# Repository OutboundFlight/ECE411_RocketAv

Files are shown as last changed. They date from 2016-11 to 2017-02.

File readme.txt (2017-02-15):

Overview:

This GitHub provides documentation for the design, implemation, and use of the TinyAV
Amateur Avionics System. The TinyAV is a printed circuit board that includes a 
microcontroller, acellerometer, gyroscope, temperature sensor, flash
memory storage, and a rechargeable lithium-ion battery. It allows for a portable way 
to record flight data that can be use for flight analysis on model rockets.

----------------------------------------------------------------------------------------------

Table Of Contents:

Assignments - Team exercises assigned in ECE 411
Doc         - Project Proposals, Project Requirements, UML Diagrams, Testing Documentation, 
	      Project Schedules, & Bill Of Materials
Eagle       - Schematic & Board Layout Documentation
Launch_Data - Test Launch Raw Data & Analysis Graphs
Ref	    - Reference Documentation For Board Creation
Src	    - Libraries & Source Code For The TinyAv Board

----------------------------------------------------------------------------------------------

Useful Links:

Lab for Interconnected Devices: http://psu-epl.github.io/
Arduino Software: https://www.arduino.cc/

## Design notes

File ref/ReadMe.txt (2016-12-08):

Raw Setup:
-------------------------------------------------------------------------------------------------------------
PCB Creation:

1) In Eagle, use DRC > Masks to set Cream min to 5.5 mil and max to 7mil.Make sure this actually adjusts cream field sizes! 
   The comparator footprint in the TI library is wronng.
2) Export to gerber files.  Use the cream gerber layer to create the stencil.
3) Use the Full Spectrum Professional Series CO2 20x12 Laser to vector cut.
	Laser Settings:
	Vector Speed: 80%
	Vector Current: 20%
	Power: 0.2%
4) Line up stencil on board and secure.  Apply solder paste on PCB using the stencil as aid. 
	Tips: 
	1) Take the syringe tip off of the solder paste syringe
	2) Spread ~2-3 lines of solder paste, just above the stencil
	3) Using a Solder Spreader card, slowly spread the paste over the board (try to only swipe once!)
5) Place components.
6) Use the Torch T200N Reflow Oven to melt solder paste and secure components.

References:

Laser Cutter: https://github.com/psu-epl/psu-epl.github.com/wiki/Lasercutter
Reflow Oven:  https://github.com/psu-epl/psu-epl.github.com/wiki/Torch-T200N-Reflow-Oven 
-------------------------------------------------------------------------------------------------------------
Bootloader:

1) Plug in Dragon AVR (Located in FAB60-04).
2) Open AtmelStudio.
3) Under Tools, go to Device Programming.
4) Select DragonAVR-Atmega32U4-ISP.
5) Apply.
6) Click Check and verify the voltage.
7) Go to Memory-Flash.
8) Browse for Caterina-lilypadusb.hex in given GitHub folder.
9) Click Program.
10) After programming, go to Fuse and set the fuses to the following:
	Extended byte: 0xCE
	High byte:     0xD0
	Low byte:      0xFF
11) Go to Lock Bit and set it to 0xFF.
12) The bootloader should now be on the TinyAv.
-------------------------------------------------------------------------------------------------------------
Programming:

1) Once bootloader is on TinyAv, it can now be plugged into a USB port (via MicroUSB).
2) Under Device Manager in Windows, the TinyAV should be seen as a port named Lilypad USB.
3) Arduino IDE sketches can now be uploaded to the TinyAV using:
	Board: Arduino USB
	Port: Lilypad USB (COMX)
	Programmer: AVRISP mkll
4) Go to Sketch>Include Library and include the the 3 .zip libraries located in the src folder:
	Adafruit_LSM9DS0_Library-master.zip
	Adafruit_Sensor-master.zip
	tinyav.zip
5) Go to File>Open and open the RocketAv arduino sketch located in the src folder.
6) Ensure the Lilypad is powered on, plugged in via microUSB, and is detected under Tools>Ports
7) Upload the sketch on Arduino IDE
--------------------------------------------------------------------------------------------------------------
Launch Procedure:

1) Set up rocket
2) Turn on the tinyav board. Connect to USB port.
3) Get IMU sample data:
	Ensure xm is calibrated correctly (1g should be about integer 2000)
	Check sample rate
4) Upload correct sketch:
	Ensure the arduino sketch is not in debug mode
	Set a launch countdown timer in the sketch
5) Erase the memory chip
6) Insert motor with igniter. 
7) Set the arduino into launch mode. Start a stopwatch.
8) Detach the USB cable.
9) Place the tinyav board in the rocket.
10) Attach ignition control leads to igniter leads.
11) Clear launch zone.
12) Launch.

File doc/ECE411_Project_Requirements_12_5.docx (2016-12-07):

Tiny Avionics

PRODUCT DESIGN SPECIFICATION

Version 3.0

12/06/2016

Aaron Baker, Andy Rusinek, Daniel Schaeffer, Minh-Nhut Dang

REVISION HISTORY
REVISION | DESCRIPTION | DATE
1.0 | INITIAL RELEASE | 10/25/2016
2.0 | PROJECT NAME CHANGE | 12/01/2016
3.0 | UPDATED REQUIREMENTS TEXT | 12/06/2016

TABLE OF CONTENTS

1 PROJECT OVERVIEW

1.1 BACKGROUND

1.2 OVERVIEW

2 REQUIREMENTS

2.1 FUNCTIONALITY

2.2 PHYSICAL RESTRICTIONS

2.3 DOCUMENTATION

2.4 ECONOMICS

2.5 MARKETING

2.6 GENERAL

1 PROJECT OVERVIEW

1.1 BACKGROUND

This project will develop a rocket avionics system for small model rockets. After we design a working version, we plan to create sellable kits which others becoming interested in amateur rocketry can use. On the system, we will have sensors for attitude and acceleration during flight, which will be processed on board and stored in a memory chip. The data will be retrievable after flight, and can then be processed on a computer and displayed visually.

1.2 OVERVIEW

The goal of our project is to create a small flight computer which can collect data in flight and store it for later analysis. To achieve this, we will use a micro-processor with the Arduino bootloader, an accelerometer, gyroscope, and an on-board flash memory chip. During flight, the gyroscope and accelerometer will gather data and save data to the onboard flash-memory chip. After flight, data will be able to be pulled off the flash memory and viewed through programs such as MATLAB and Excel. The system will be powered by a single rechargeable lithium-ion cell.

2 REQUIREMENTS

2.1 FUNCTIONALITY:

- Deploy recovery system for reusability of rocket and board.
- Accurately sense acceleration, attitude, and rotation to at least 3 significant digits
- Must have ample power management to last at least 10 consecutive 30 second flights.
- Record flight data at a sample rate of 1 kHz (acceleration, attitude, rotation) for retrieval after flight
- Be able to transfer data to computer for processing and display

2.2 PHYSICAL RESTRICTIONS:

- Must be 1x3 inches or smaller to fit inside rocket nose
- Durable through indefinite number of uses and crash landings
- Easily removed and reinserted into different type of rocket noses

2.3 DOCUMENTATION:

- Thoroughly documented schematics, PCB layouts, and design sketches with revision tracking
- General test plan for basic functionality of accelerometer and gyroscope
- Comprehensive User’s Manual for device operation and set-up

2.4 ECONOMICS:

- Total cost under $60
- Must use easy to obtain parts from reputable vendor

2.5 MARKETING

- Boards assembled easily and cheaply
- Easy to use built in test-programs and Arduino libraries for code development
- Raw data easily converted to visual in form of 2-D or 3-D plot
- Have LED indications of functioning parts

2.6 GENERAL

- Be visually appealing
- Be expandable
- Integratable into other amateur rocketry systems

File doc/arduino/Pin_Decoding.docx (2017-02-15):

Look at pin name on ATMEGA32U4 (i.e. PF1… PF0… ETC)

Find the pin name on the LEONARDO PINOUT picture

Find the Pin on the physical leonardo board corresponding with the PIN you want to decode…

I.e: PF0 = A5.

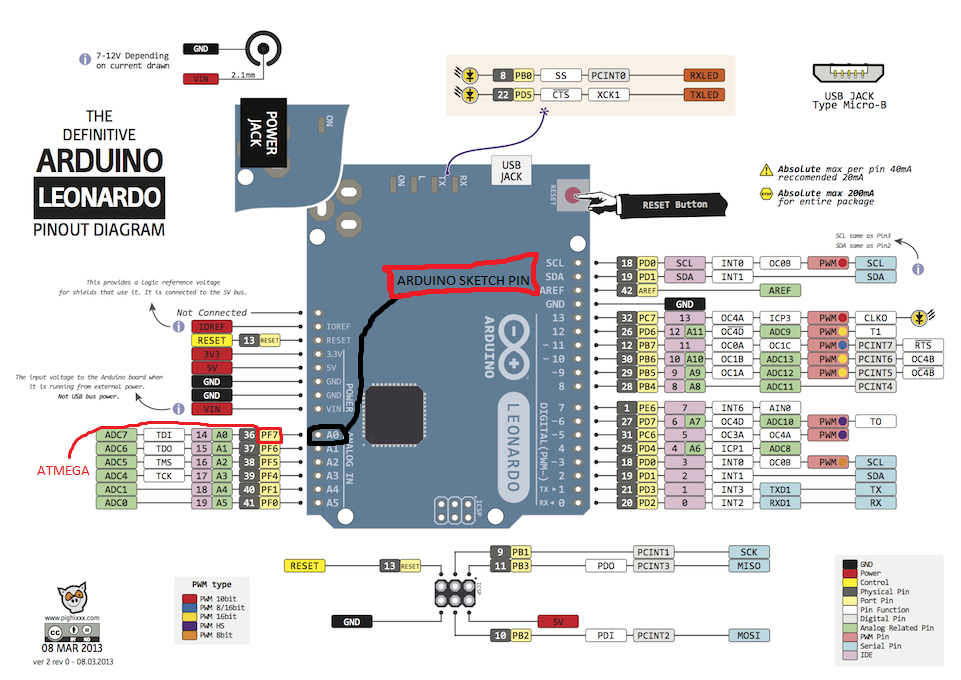
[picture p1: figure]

ATMEGA32U4 | ARDUINO SKETCH PIN NAME
MISO | 14
MOSI | 15
SCLK | 16
MEM_EN (PF1) | A4 (22)
XM_EN (PF4) | A3
GYR_EN (PF5) | A2
RED_LED (PB6) | 10
GREEN_LED (PB5) | 9
BLUE_LED (PB4) | 8

0xCE

0xD0

0xFF

0xFF

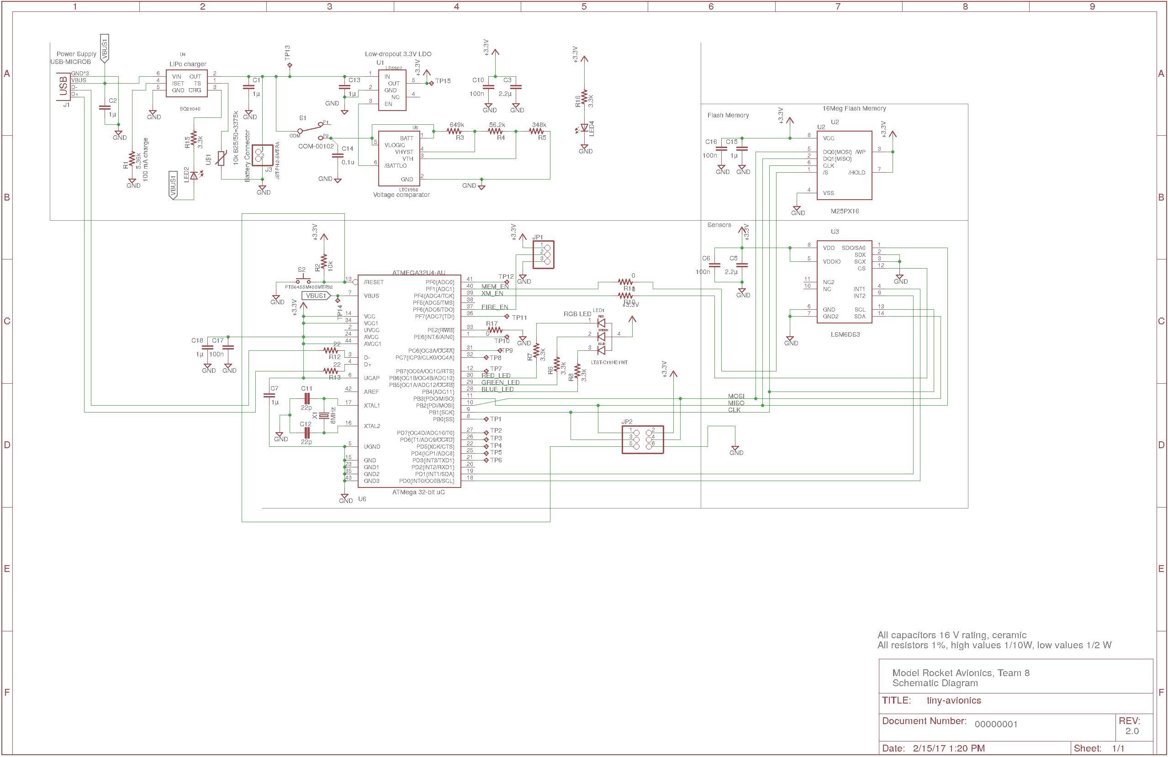
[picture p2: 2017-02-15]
eagle/schematic.png

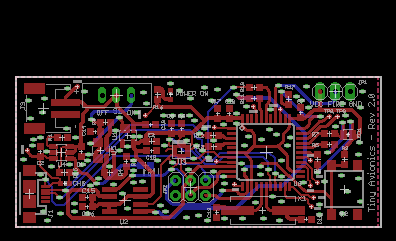
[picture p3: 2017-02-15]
eagle/board.png

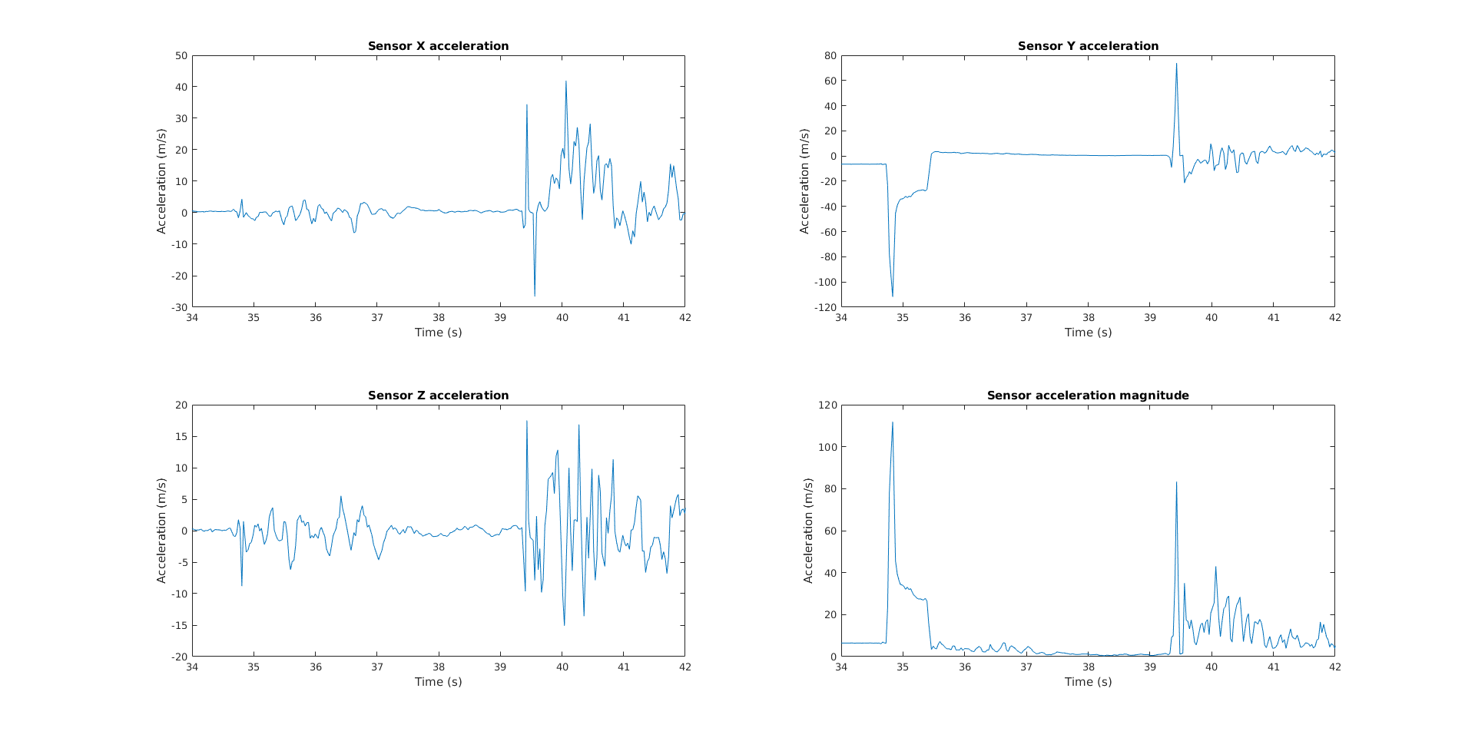
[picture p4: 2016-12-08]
launch_data/Launch 12-08-16/launch1_accel.png

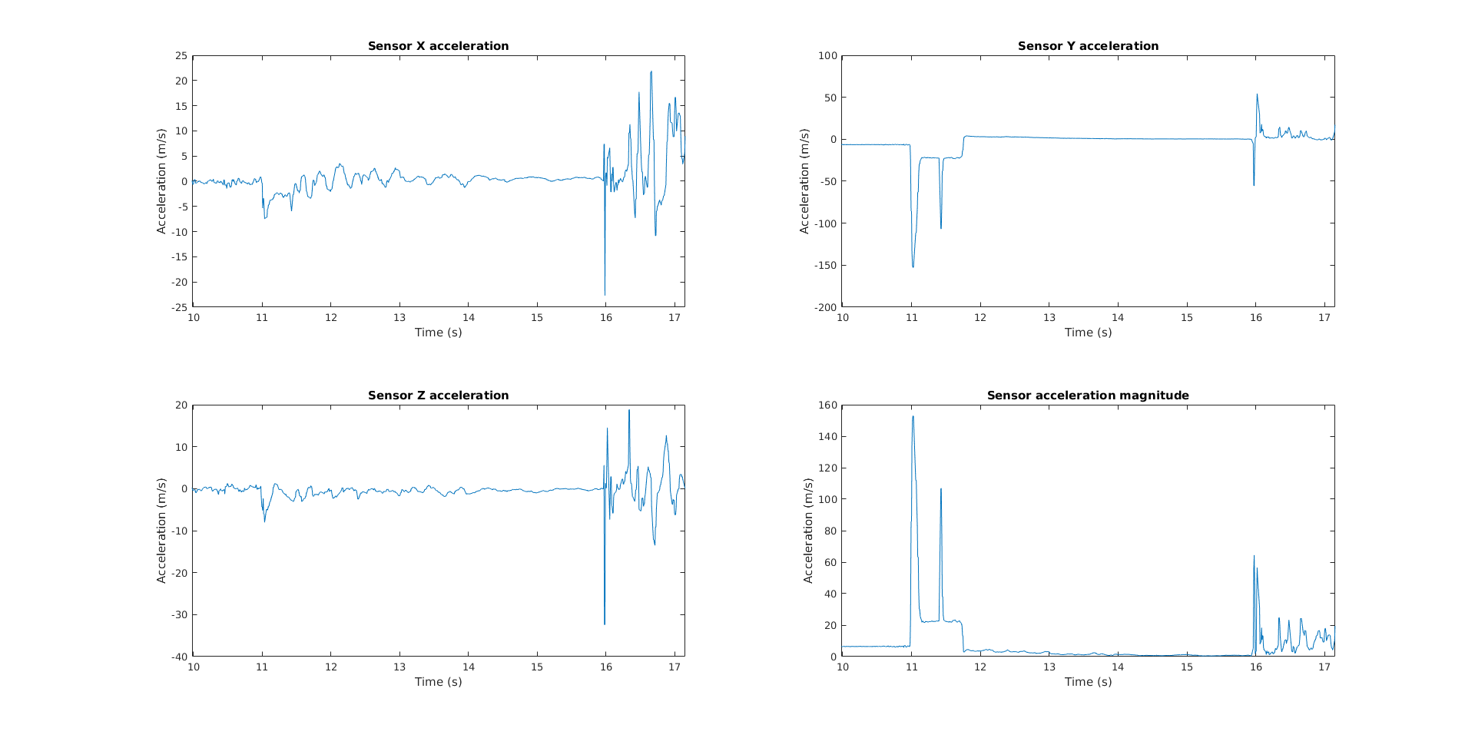
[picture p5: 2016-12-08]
launch_data/Launch 12-08-16/launch3_accel.png

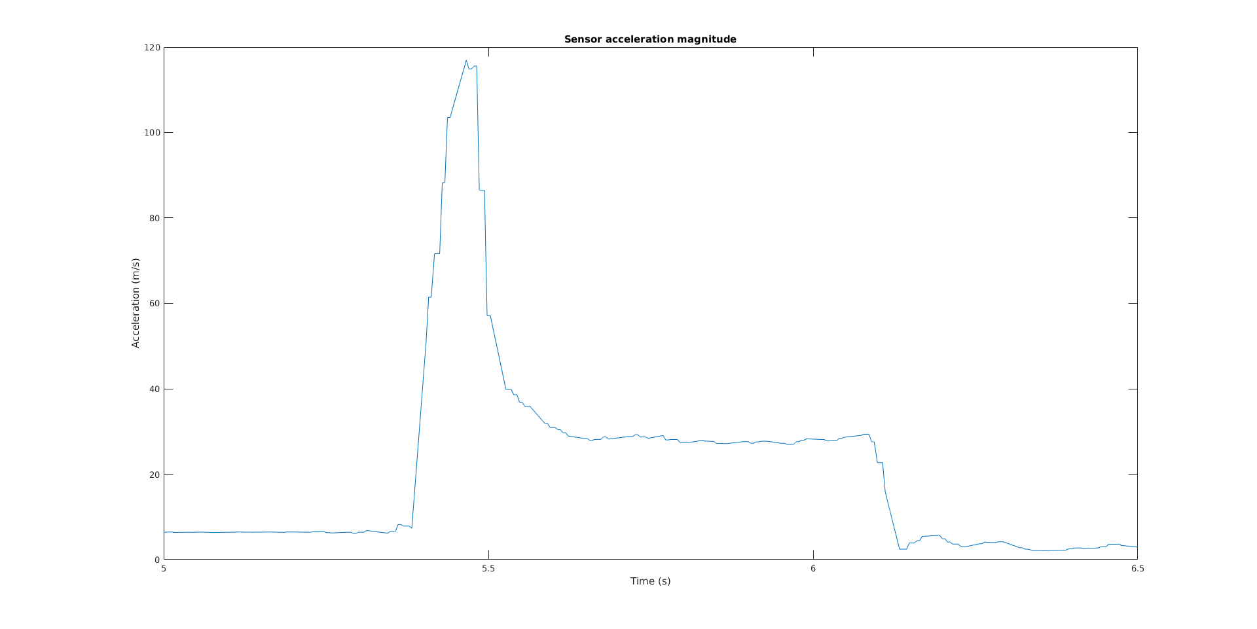
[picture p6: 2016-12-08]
launch_data/Launch 12-08-16/launch4_thrustcurve.png

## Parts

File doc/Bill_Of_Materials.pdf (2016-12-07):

QUANTITY/BRD | REF DES | DESCRIPTION | VENDOR | VENDOR_PN | PRICE(EA) (USD) | TOTAL
6 | C1, C2, C7, C13, C15, C18 | CAP CER 1UF 16V Y5V 0603 | DIGIKEY | 311-1372-1-ND | $0.10 | $0.60
2 | C11, C12 | CAP CER 22PF 16V NP0 0603 | DIGIKEY | 399-9031-1-ND | $0.10 | $0.20
1 | C3 | CAP CER 4.7UF 16V X5R 0603 | DIGIKEY | 587-2786-1-ND | $0.38 | $0.38
1 | C4 | CAP CER 0.22UF 16V X7R | DIGIKEY | 445-1318-1-ND | $0.10 | $0.10
2 | C5, C9 | CAP CER 2.2UF 16V Y5V 0603 | DIGIKEY | 587-1263-1-ND | $0.28 | $0.56
5 | C6, C10, C14, C16, C17 | CAP CER 0.1UF 16V X7R 0603 | DIGIKEY | 311-1088-1-ND | $0.10 | $0.50
1 IC1 | | IC LI-ION/LI-POL CHARGER 10-SON | DIGIKEY | 296-14397-1-ND | $2.97 | $2.97
1 | J1 | USB-MICROB | SPARKFUN | PRT-08533 | $1.50 | $1.50
1 | J3 | 455-1578-1-ND | DIGIKEY | 455-1578-1-ND | $0.43 | $0.43
1 JP1 | | 3 Positions Header, Unshrouded Throughhole | DIGIKEY | 952-2264-ND | $0.15 | $0.15
1 JP2 | | 6 Positions Header, Unshouded Throughhole | DIGIKEY | 952-2121-ND | $0.24 | $0.24
1 LED1 | | LED RGB DIFFUSED 0606 SMD | DIGIKEY | 160-2162-1-ND | $0.59 | $0.59
1 | LED2 | BLue 470nm LED Indication | DIGIKEY | 160-1827-1-ND | $0.47 | $0.47
1 | LED3 | Green 572nm LED Indcation | DIGIKEY | 160-1828-1-ND | $0.41 | $0.41
1 | LED4 | Yellow 591nm LED Indcation | DIGIKEY | 160-1831-1-ND | $0.41 | $0.41
1 | R1 | RES SMD 3.9K OHM 5% | DIGIKEY | 311-3.9KGRCT-ND | $0.10 | $0.10
2 | R12, R13 | RES SMD 22 OHM 5% | DIGIKEY | 311-22GRCT-ND | $0.10 | $0.20
3 | R14, R15, R16 | RES SMD 1K OHM 5% 1/10W | DIGIKEY | 311-1.0KGRCT-ND | $0.10 | $0.30
1 | R2 | RES SMD 10K OHM 5% 1/10W | DIGIKEY | 311-10KGRCT-ND | $0.10 | $0.10
1 R3 | | RES SMD 649K OHM 1% 1/10W | DIGIKEY | 311-649KHRCT-ND | $0.10 | $0.10
1 R4 | | RES SMD 56.2K OHM 1% 1/10W | DIGIKEY | 311-56.2KHRCT-ND | $0.10 | $0.10
1 R5 | | RES SMD 348K OHM 1% 1/10W | DIGIKEY | 311-348KHRCT-ND | $0.10 | $0.10
3 | R6, R7, R8 | RES SMD 300 OHM 5% 0.4W | DIGIKEY | RHM300KCT-ND | $0.10 | $0.30
4 R9, R10, R11, R17 | | RES SMD 0.0OHM JUMPER 1/10W | DIGIKEY | 311-0.0GRCT-ND | $0.10 | $0.40
1 | S1 | SPDT Switch | SPARKFUN | COM-00102 | $1.50 | $1.50
1 S2 | | SWITCH TACTILE SPST-NO 0.05A 12V | DIGIKEY | CKN9112CT-ND | $0.15 | $0.15
1 | U1 | Linear Voltage Regulator IC | DIGIKEY | 296-38557-1-ND | $0.57 | $0.57
1 | U2 | IC FLASH 1MBIT 50MHZ 8SO | DIGIKEY | M25P10-AVMN6TP CT-ND | $0.43 | $0.43
1 U3 | | IMU ACCEL/GYRO/MAG I2C/SPI 24LGA | DIGIKEY | 497-13902-1-ND | $9.19 | $9.19
1 U5 | | IC DETECT VOLT PR LOBATT SOT23-6 | DIGIKEY | LTC1998IS6#TRMPBFCT-ND | $2.93 | $2.93
1 U6 | | AVR AVR® ATmega Microcontroller IC 8-Bit 16MHz 32KB | DIGIKEY | ATMEGA32U4-AU-ND | $6.35 | $6.35
1 X1 | | 8MHz ±30ppm Crystal 18pF 60 Ohm | DIGIKEY | CTX900-ND | $0.36 | $0.36
1 | BAT (external) | Lithium Ion Battery - 110mAh | SPARKFUN | PRT-13853 ROHS | $4.95 | $4.95
TOTAL COST | $37.64

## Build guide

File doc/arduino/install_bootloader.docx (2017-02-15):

Plug in dragon avr connecter

Open Device Programming in AtmelStudio

Apply the Atmega32U4-ISP Settings

Go to Memory

Browse for the Caterina-LilypadUSB hex file (in the folder this document is in) or download most recent version from https://github.com/sparkfun/SF32u4_boards/tree/master/sparkfun/avr/bootloaders/caterina

Program the fuses per:
Fuse settings:

- Lock byte 0xFF
- Extended byte: 0xCE
- High byte: 0xD0
- Low byte: 0xFF

To validate the fuse settings, look at the oscillator with power turned on. It should look like an 8MHz sine wave.

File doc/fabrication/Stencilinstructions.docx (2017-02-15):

1. In Eagle, use DRC > Masks to set Cream min to 5.5 mil and max to 7mil.Make sure this actually adjusts cream field sizes! The comparator footprint in the TI library is wronnggggg, for example
2. Export to gerber file using standard procedure and print to Full Spectrum driver
3. Power settings for parchment paper stencil are vector speed 80%, power 0.2%, vector current 20%
4. Cut as a vector

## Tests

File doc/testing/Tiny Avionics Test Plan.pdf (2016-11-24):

# Tiny Avionics

## Test Plan

## Version 1.0

11/24/2016

## Team 08

## Aaron Baker, Andy Rusinek, Daniel Schaeffer, Minh-Nhut Dang

TINY AVIONICS: System

T

e

st Pl

a

n

1. INTRODUCTION
1.1. This Docume

n

t
1.2. Conduct of

t

h

e Syst

em

t

est

s
2. REFERENCE DOC

UMEN

T

S
2.1. Design Docume

n

t

a

tio

n
3. TINY AVIONICS OVERVIEW
3.1. Operational D

escri

p

tio

n
4. PRETEST PREPA

RATIO

N
4.1. Test Equipme

n

t
5. SYSTEM TESTS
5.1. Power:
5.1.1. Po

w

er Switch
5.1.2. Charg

e

/

disch

arg

e
5.1.3. Stabilit

y
5.1.4. Po

w

er co

nsump

tio

n

b

e

nchmark
5.1.5. Curre

n

t limi

tin

g
5.1.6. Ov

erch

arg

e

pro

t

ectio

n
5.1.7. Und

erch

arg

e

pro

t

ectio

n
5.2. Universal Seri

al Bus:
5.2.1. Pro

gramma

bilit

y
5.2.2. Bus sp

e

e

d
5.2.3. Charg

e

/

disch

arg

e
5.2.4. Bus

n

oise
5.3. Microcontr

oller:
5.3.1. GPIO

T

est
5.3.2. Int

erru

p

t

s
5.3.3. Clock sp

e

e

d
5.3.4. Ard

uin

o

b

e

nchmark
5.4. Serial Peri

p

h

eral In

t

erf

ace:
5.4.1. Bus sp

e

e

d
5.4.2. Bus

n

oise
5.5. Memory:
5.5.1. Writ

e sp

e

e

d
5.5.2. Bit

error ra

t

e
5.6. Sensors:
5.6.1. Accelerome

t

er calibra

tio

n
5.6.2. Gyrosco

p

e calibra

tio

n
5.6.3. Po

w

er

n

oise

t

estin

g
5.6.4. Accelerome

t

er

n

oise
5.6.5. Gyrosco

p

e

n

oise
5.6.6. Int

erru

p

t

s

5.6.7. Sample rate benchmarking
5.7. Firing Circuit:
5.7.1. Current consumption
5.7.2. Noise
5.8. Flight test
5.8.1. Recovery firing circuit
5.8.2. Durability
5.8.3. Data retrieval

## 1. INTRODUCTION

### 1.1 This Document

This document serves as a guide to detailed testing of the Tiny Avionics system and its components.

### 1.2 Conduct of System Tests

Testing of the Tiny Avionics system shall be conducted by project team members for the initial design, and further testing may be undertaken by future users of the Tiny Avionics system to verify the working condition of their own Tiny Avionics system.

## 2. REFERENCE DOCUMENTS

### 2.1 Design Documentation

All design documentation is available on the Tiny Avionics project wiki: https://github.com/rusinek/ECE411_RocketAv/wiki

## 3.TINY AVIONICS OVERVIEW

### 3.1 Operational Description

Tiny Avionics is a rocket avionics system for small model rockets. Tiny avionics is designed to be a sellable kit which others becoming interested in amateur rocketry can use. The Tiny Avionics system has sensors for attitude and acceleration during flight with data being processed on board and stored in a memory chip. The data will be retrievable after flight, and can then be processed on a computer and displayed visually.

## 4.0 PRETEST PREPARATION

### 4.1 Test Equipment

The following is the list of equipment necessary for testing the Tiny Avionics system.
- Computer with Arduino Software
- Digital Multimeter RadioShack 22-812
- Oscilloscope Tektronix TDS3034B
- Estes model rocket modified to hold Rocket Avionics system
- 0.1 ohm 1% current sense resistor

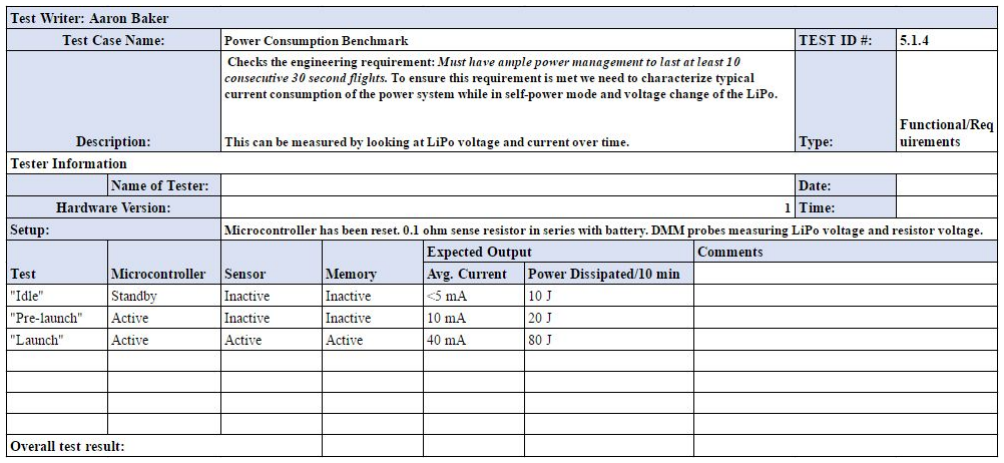
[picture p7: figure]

5.1.4

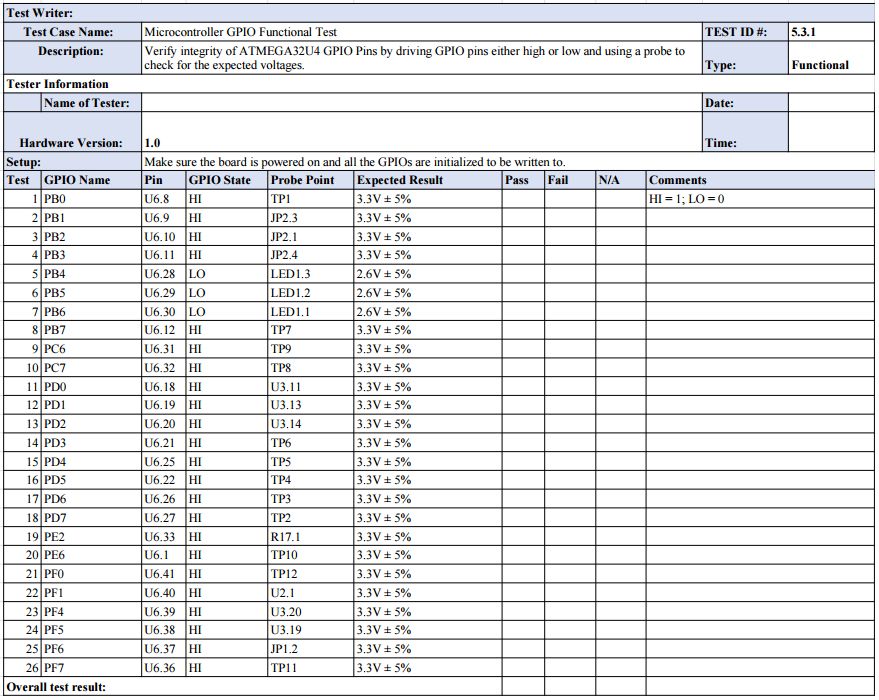
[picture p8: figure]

5.3.1

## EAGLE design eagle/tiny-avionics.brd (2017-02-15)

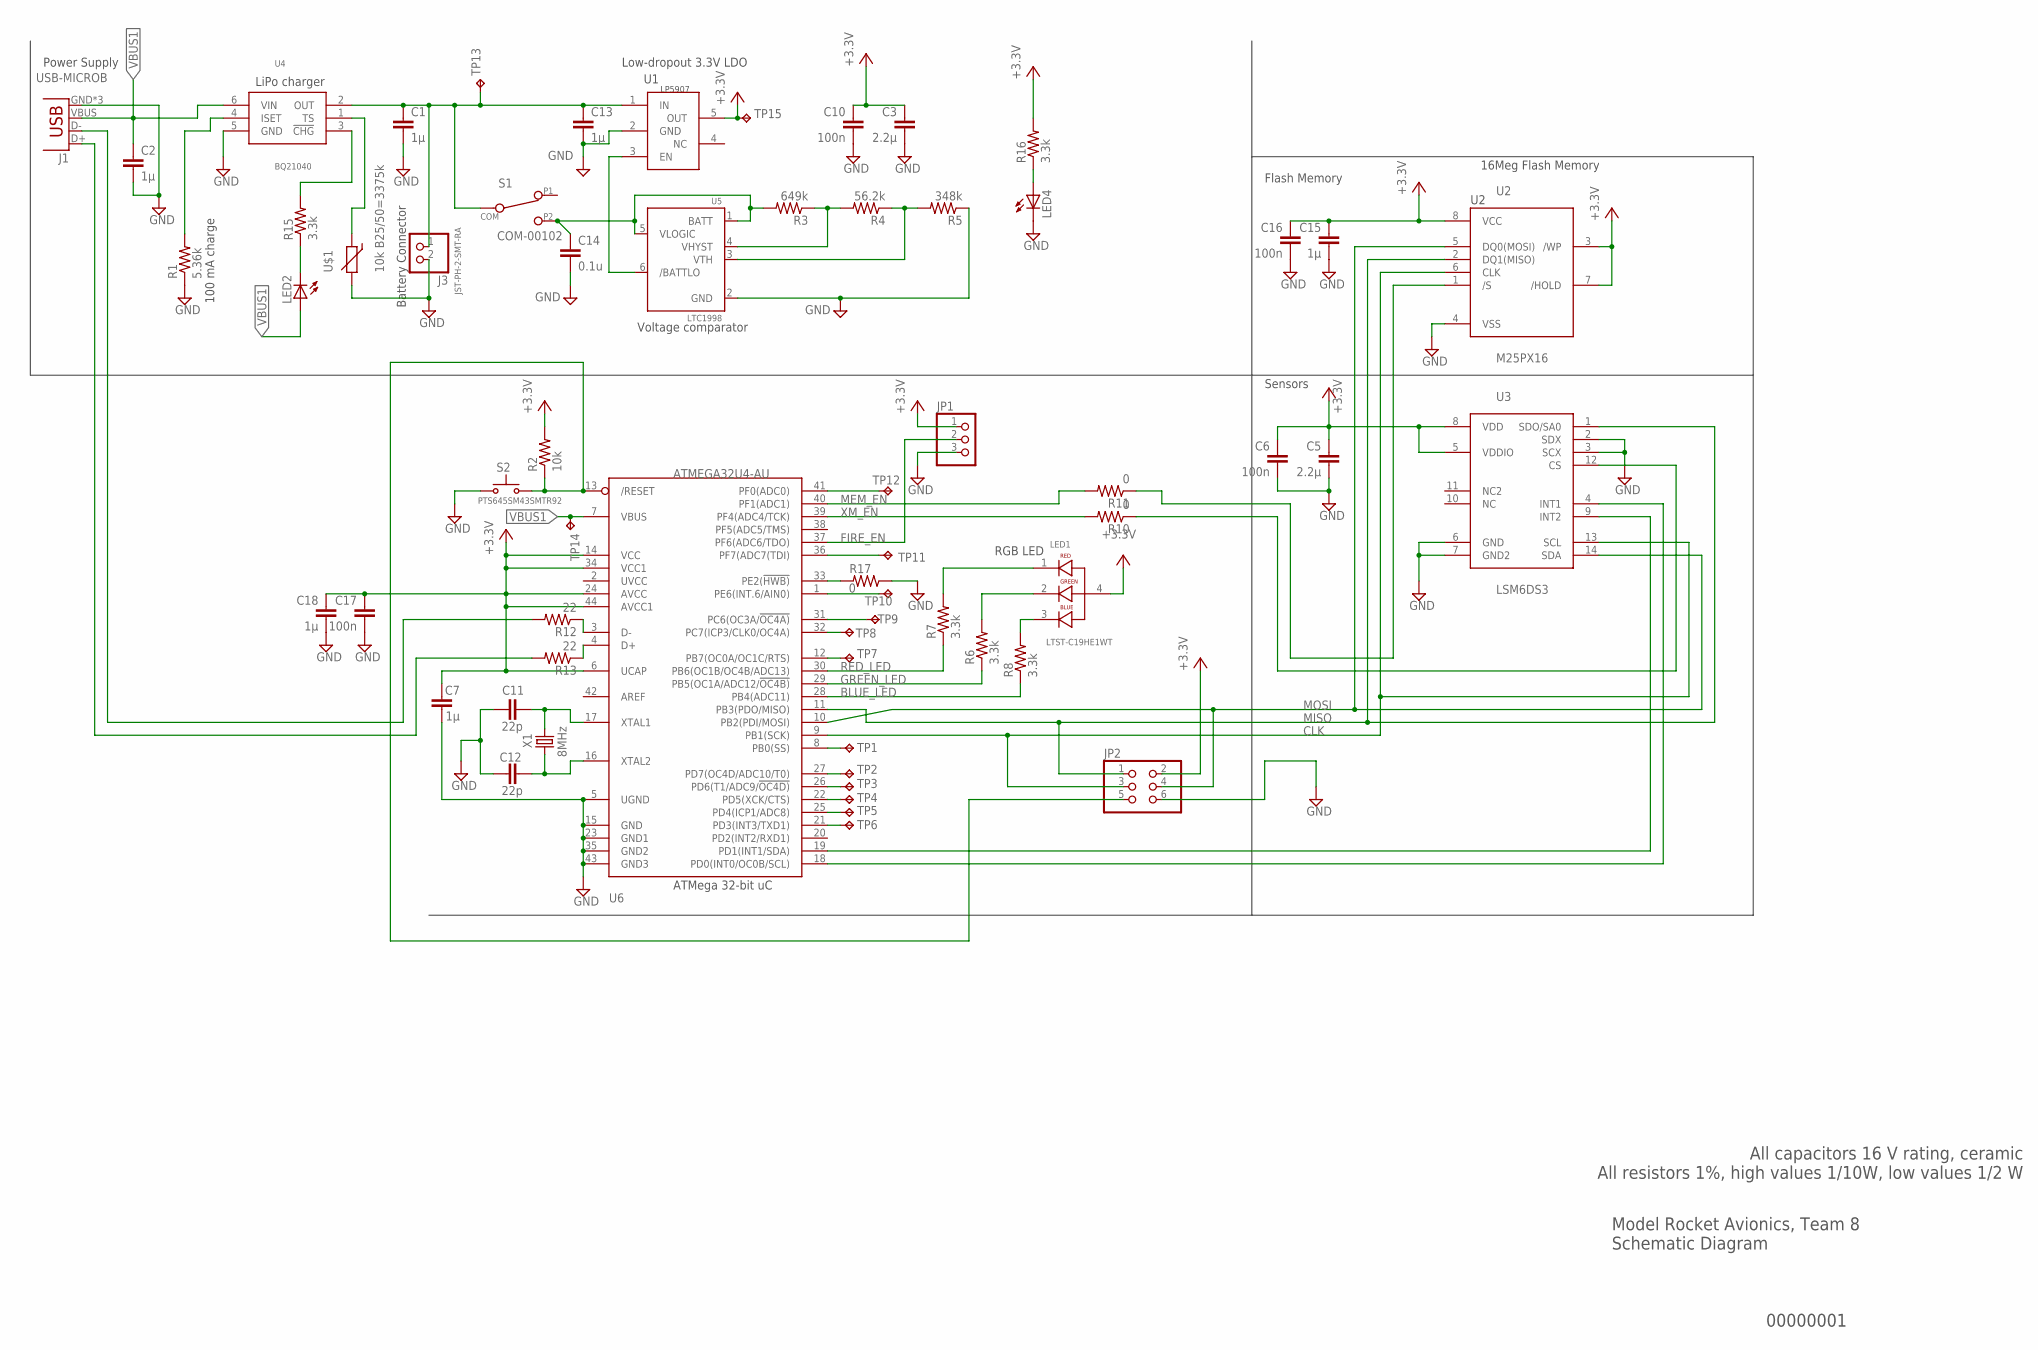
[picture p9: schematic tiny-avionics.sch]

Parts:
C1, C2, C7, C13, C15, C18: 1µ; C0603
C3, C5: 2.2µ; C0603
C6, C10, C16, C17: 100n; C0603
C11, C12: 22p; C0603
C14: 0.1u; C0603
J1: USB-MICROB
J3: JST-PH-2-SMT-RA
JP1: PINHD-1X3; 1X03
JP2: PINHD-2X3; 2X03
LED1: LTST-C19HE1WT; LEDSC85P160X160X35-4N
LED2, LED4: LEDCHIP-LED0603; CHIP-LED0603
R1: 5.36k; R0603
R2: 10k; R0603
R3: 649k; R0603
R4: 56.2k; R0603
R5: 348k; R0603
R6, R7, R8, R15, R16: 3.3k; R0603
R10, R11, R17: 0; R0603
R12, R13: 22; R0603
S1: COM-00102; ESWITCH
S2: PTS645SM43SMTR92; PTS645-SMD; MPN PTS645SM43SMTR92 LFS
TP1, TP2, TP3, TP4, TP5, TP6, TP7, TP8, TP9, TP10, TP11, TP12, TP13, TP14, TP15: TPTP08R; TP08R
U1: LP5907; SOT23-5L
U2: M25PX16; SO8
U3: LSM6DS3; LGA-14L
U4: BQ21040; SOT23-6L
U5: LTC1998; TSOT23-6
U6: ATMEGA32U4-AU; TQFP44
U$1: 10k B25/50=3375k; R0603
X1: 8MHz; ATS-SM; MPN ATS080B

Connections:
BLUE_LED: R8.1, U6.28 (PB4(ADC11))
CLK: JP2.3, U2.6 (CLK), U3.13 (SCL), U6.9 (PB1(SCK))
D+: J1.D+, R13.2
D-: J1.D-, R12.2
FIRE_EN: JP1.2, U6.37 (PF6(ADC6/TDO))
GND: C1.2, C2.2, C3.2, C5.2, C6.2, C7.2, C10.2, C11.2, C12.2, C13.2, C14.2, C15.2, C16.2, C17.2, C18.2, J1.GND, J1.MT1 (GND), J1.MT2 (GND), J3.2 (1), JP1.3, JP2.6, LED4.C, R1.1, R5.1, R17.1, S2.1, S2.2, U1.2 (GND), U2.4 (VSS), U3.2 (SDX), U3.3 (SCX), U3.6 (GND), U3.7 (GND2), U4.5 (GND), U5.2 (GND), U6.5 (UGND), U6.15 (GND), U6.23 (GND1), U6.35 (GND2), U6.43 (GND3), U$1.2
GREEN_LED: R6.1, U6.29 (PB5(OC1A/ADC12/!OC4B))
MEM_EN: R11.1, U2.1 (/S)
MISO: JP2.1, U2.2 (DQ1(MISO)), U3.1 (SDO/SA0), U6.11 (PB3(PDO/MISO))
MOSI: JP2.4, U2.5 (DQ0(MOSI)), U3.14 (SDA), U6.10 (PB2(PDI/MOSI))
unnamed: LED1.1, R7.2
unnamed: C11.1, U6.17 (XTAL1), X1.1
unnamed: JP2.5, R2.1, S2.3 (S), S2.4 (S), U6.13 (/RESET)
unnamed: R15.2, U4.3 (!CHG)
unnamed: C12.1, U6.16 (XTAL2), X1.2
unnamed: R12.1, U6.3 (D-)
unnamed: LED1.2, R6.2
unnamed: LED1.3, R8.2
unnamed: U4.1 (TS), U$1.1
unnamed: U3.4 (INT1), U6.18 (PD0(INT0/OC0B/SCL))
unnamed: U3.9 (INT2), U6.19 (PD1(INT1/SDA))
unnamed: R3.1, R4.2, U5.4 (VHYST)
unnamed: C1.1, C13.1, J3.1 (2), S1.2 (COM), TP13.TP, U1.1 (IN), U4.2 (OUT)
unnamed: R4.1, R5.2, U5.3 (VTH)
unnamed: C14.1, R3.2, S1.3 (P2), U5.1 (BATT), U5.5 (VLOGIC)
unnamed: U1.3 (EN), U5.6 (/BATTLO)
unnamed: R10.2, U6.39 (PF4(ADC4/TCK))
unnamed: R11.2, U6.40 (PF1(ADC1))
unnamed: R13.1, U6.4 (D+)
unnamed: LED2.C, R15.1
unnamed: R1.2, U4.4 (ISET)
unnamed: LED4.A, R16.1
unnamed: R17.2, U6.33 (PE2(!HWB))
RED_LED: R7.1, U6.30 (PB6(OC1B/OC4B/ADC13))
TP1: TP1.TP, U6.8 (PB0(SS))
TP2: TP2.TP, U6.27 (PD7(OC4D/ADC10/T0))
TP3: TP3.TP, U6.26 (PD6(T1/ADC9/!OC4D))
TP4: TP4.TP, U6.22 (PD5(XCK/CTS))
TP5: TP5.TP, U6.25 (PD4(ICP1/ADC8))
TP6: TP6.TP, U6.21 (PD3(INT3/TXD1))
TP7: TP7.TP, U6.12 (PB7(OC0A/OC1C/RTS))
TP8: TP8.TP, U6.32 (PC7(ICP3/CLK0/OC4A))
TP9: TP9.TP, U6.31 (PC6(OC3A/!OC4A))
TP10: TP10.TP, U6.1 (PE6(INT.6/AIN0))
TP11: TP11.TP, U6.36 (PF7(ADC7(TDI))
TP12: TP12.TP, U6.41 (PF0(ADC0))
VBUS1: C2.1, J1.VBUS, LED2.A, TP14.TP, U4.6 (VIN), U6.7 (VBUS)
VCC: C3.1, C5.1, C6.1, C7.1, C10.1, C15.1, C16.1, C17.1, C18.1, JP1.1, JP2.2, LED1.4, R2.2, R16.2, TP15.TP, U1.5 (OUT), U2.3 (/WP), U2.7 (/HOLD), U2.8 (VCC), U3.5 (VDDIO), U3.8 (VDD), U6.6 (UCAP), U6.14 (VCC), U6.24 (AVCC), U6.34 (VCC1), U6.44 (AVCC1)
XM_EN: R10.1, U3.12 (CS)

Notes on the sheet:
00000001
Model Rocket Avionics, Team 8 Schematic Diagram
Power Supply
Sensors
Flash Memory
All capacitors 16 V rating, ceramic All resistors 1%, high values 1/10W, low values 1/2 W
Battery Connector
Low-dropout 3.3V LDO
Voltage comparator
LiPo charger
ATMega 32-bit uC
16Meg Flash Memory
RGB LED
100 mA charge

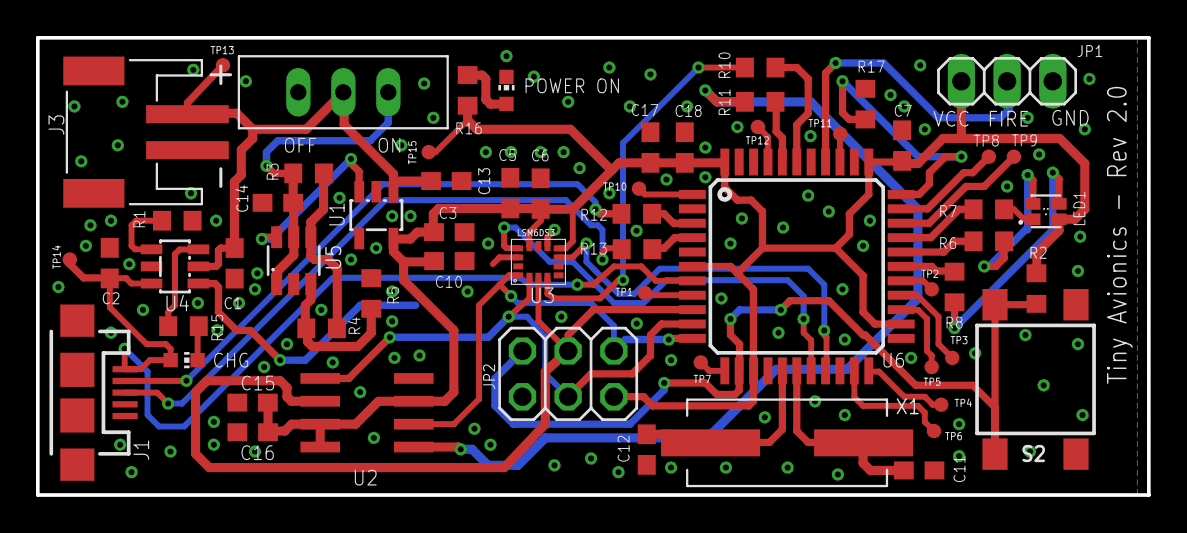
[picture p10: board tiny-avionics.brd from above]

Board: 2 copper layers, 61.7 x 25.4 mm, 62 parts (1 on the bottom side), 49 nets.

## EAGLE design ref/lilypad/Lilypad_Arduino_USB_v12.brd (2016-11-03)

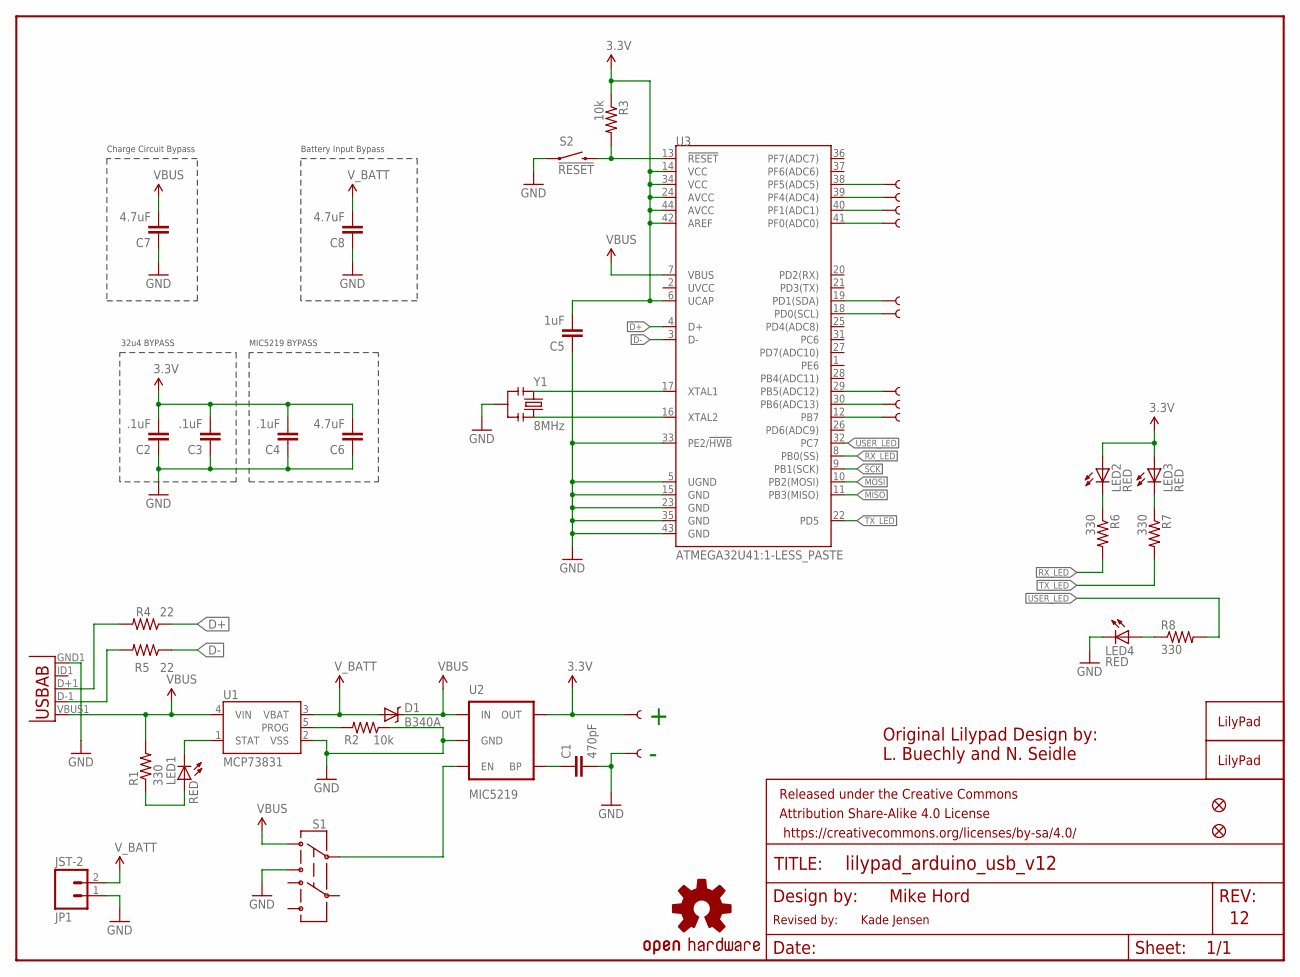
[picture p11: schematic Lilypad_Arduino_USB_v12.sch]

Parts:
+: SEWTAP9; PETAL-LONG-1-2SIDE
-: SEWTAP9; PETAL-LONG-1-2SIDE
A2, A3, A4, A5: SEWTAP9; PETAL-LONG-1-2SIDE
C1: 470pF; 0603-CAP
C2, C3, C4: .1uF; 0603-CAP
C5: 1uF; 0603-CAP
C6: 4.7uF; 0603-CAP
C7, C8: 4.7uF; 1206
D1: B340A; SMA-DIODE
D5, D6, D9, D10, D11: SEWTAP9; PETAL-LONG-1-2SIDE
FRAME1: FRAME-LETTER; CREATIVE_COMMONS
JP1: JST-2; JST-2-SMD
JP2, JP3: FIDUCIAL1X2; FIDUCIAL-1X2
LED1, LED2, LED3, LED4: RED; LED-0603
R1, R6, R7, R8: 330; 0603-RES
R2, R3: 10k; 0603-RES
R4, R5: 22; 0603-RES
S1: SWITCH-DPDTAYZ0202; AYZ0202
S2: !RESET; TACTILE_SWITCH_SMD
U1: MCP73831; SOT23-5
U2: MIC5219; SOT23-5
U3: ATMEGA32U41:1-LESS_PASTE; QFN-44-NOPAD_1:1-LESS_PASTE
U5: USB-ABCONN-11794; USB-AB-MICRO-SMD_V03
U$1: LOGO-LPLPA; LOGO-LPA
U$5: OSHW-LOGOM; OSHW-LOGO-M
U$13: LOGO-LPLP; LOGO-LILYPAD
Y1: 8MHz; RESONATOR-SMD

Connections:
3.3V: +.1, C2.2, C3.2, C4.2, C5.2, C6.2, LED2.A, LED3.A, R3.1, U2.5 (OUT), U3.6 (UCAP), U3.14 (VCC), U3.24 (AVCC), U3.34 (VCC), U3.42 (AREF), U3.44 (AVCC)
5V: C7.2, D1.C, R1.2, S1.1, U1.4 (VIN), U2.1 (IN), U3.7 (VBUS), U5.VBUS1 (VBUS)
D+: R4.1, U3.4 (D+)
D-: R5.1, U3.3 (D-)
GND: -.1, C1.2, C2.1, C3.1, C4.1, C5.1, C6.1, C7.1, C8.1, JP1.1 (2), LED4.C, R2.1, S1.3, S2.1, U1.2 (VSS), U2.2 (GND), U3.5 (UGND), U3.15 (GND), U3.23 (GND), U3.33 (PE2/!HWB), U3.35 (GND), U3.43 (GND), U5.GND1 (GND), Y1.2
MISO: U3.11 (PB3(MISO))
MOSI: U3.10 (PB2(MOSI))
unnamed: LED2.C, R6.1
unnamed: S1.2, U2.3 (EN)
unnamed: LED1.A, R1.1
unnamed: LED1.C, U1.1 (STAT)
unnamed: U3.17 (XTAL1), Y1.1
unnamed: R2.2, U1.5 (PROG)
unnamed: U3.16 (XTAL2), Y1.3
unnamed: C1.1, U2.4 (BP)
unnamed: D11.1, U3.12 (PB7)
unnamed: D10.1, U3.30 (PB6(ADC13))
unnamed: D9.1, U3.29 (PB5(ADC12))
unnamed: D5.1, U3.19 (PD1(SDA))
unnamed: D6.1, U3.18 (PD0(SCL))
unnamed: A5.1, U3.41 (PF0(ADC0))
unnamed: A4.1, U3.40 (PF1(ADC1))
unnamed: A3.1, U3.39 (PF4(ADC4))
unnamed: A2.1, U3.38 (PF5(ADC5))
unnamed: LED4.A, R8.1
unnamed: R5.2, U5.D-1 (D-)
unnamed: R4.2, U5.D+1 (D+)
unnamed: LED3.C, R7.1
RESET: R3.2, S2.3 (2), U3.13 (!RESET)
RX_LED: R6.2, U3.8 (PB0(SS))
SCK: U3.9 (PB1(SCK))
TX_LED: R7.2, U3.22 (PD5)
USER_LED: R8.2, U3.32 (PC7)
V_BATT: C8.2, D1.A, JP1.2 (1), U1.3 (VBAT)

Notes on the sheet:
32u4 BYPASS
MIC5219 BYPASS
Mike Hord
Original Lilypad Design by:
L. Buechly and N. Seidle
Charge Circuit Bypass
Battery Input Bypass
Revised by:
Kade Jensen

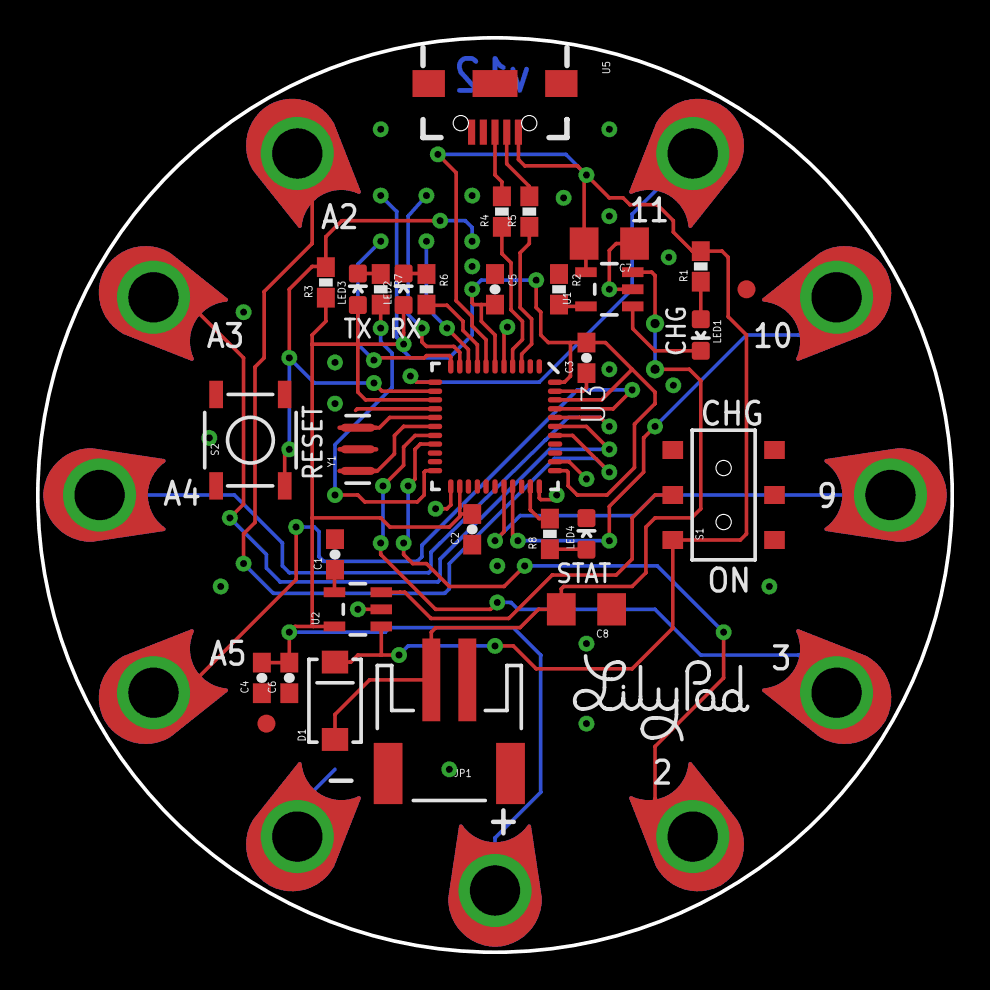
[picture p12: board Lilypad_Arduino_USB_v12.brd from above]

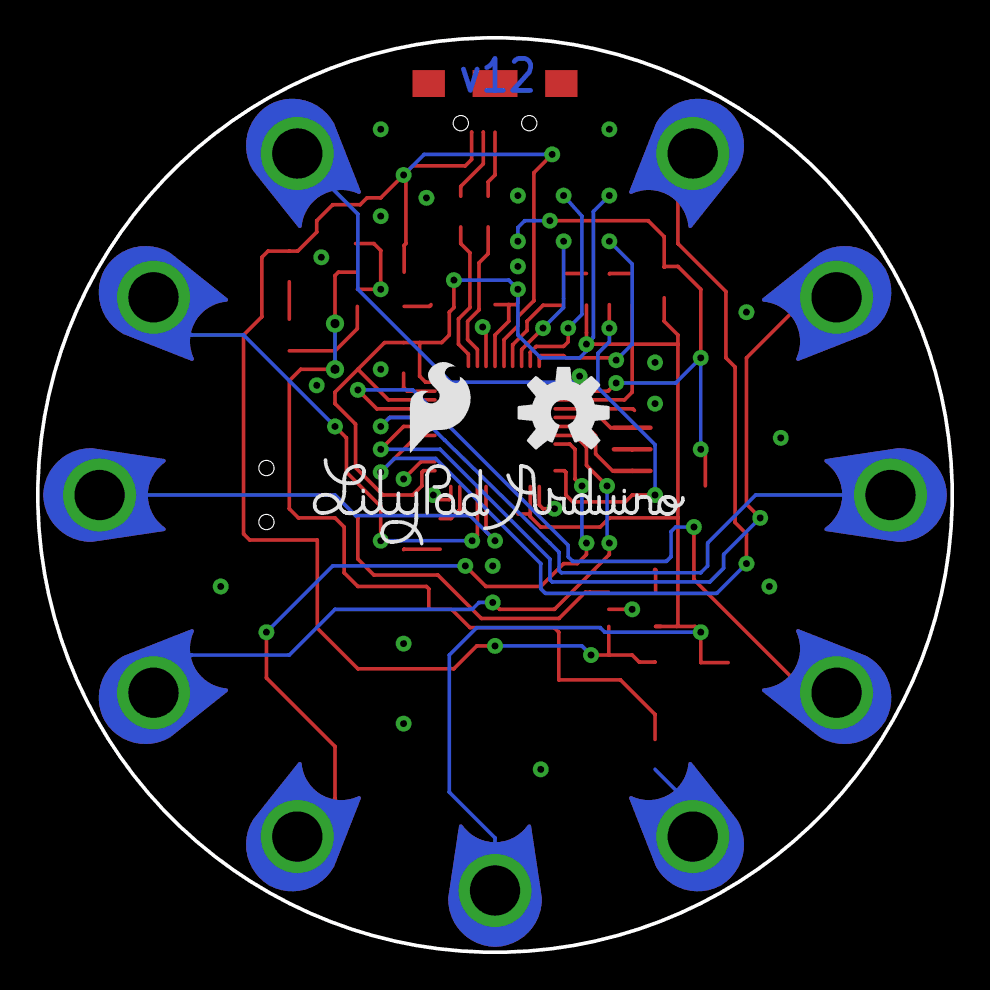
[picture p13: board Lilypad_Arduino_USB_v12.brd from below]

Board: 2 copper layers, 50.8 x 50.8 mm, 47 parts (3 on the bottom side), 31 nets.

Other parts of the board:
U$7: SFE_LOGO_FLAME_.2

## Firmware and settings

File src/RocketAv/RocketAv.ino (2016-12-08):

#include <SPI.h>
#include <Adafruit_LSM9DS0.h>
#include <Adafruit_Sensor.h>
#include <tinyav_spiflash.h>

#define SENSOR_STALL 2

//#define SERIAL_DEBUG

// Define enable pins
#define MEM_EN 22
#define GYR_EN A2
#define XM_EN A3

#define BAUD 115200

// Hardware SPI setup for sensor
Adafruit_LSM9DS0 lsm = Adafruit_LSM9DS0(XM_EN, GYR_EN);

typedef struct sensor_sample {
  long timestamp;
  int xm_x;
  int xm_y;
  int xm_z;
  int gyr_x;
  int gyr_y;
  int gyr_z;
  int mag_x;
  int mag_y;
  int mag_z;
  int temp;
  char line;
}sensor_sample;

int samples_per_page = PAGE_SIZE/sizeof(sensor_sample);

union page
{
  sensor_sample entries[12];
  uint8_t bytes [PAGE_SIZE];
} pdata;

void setupSensor()
{
  // 1.) Set the accelerometer range
  //lsm.setupAccel(lsm.LSM9DS0_ACCELRANGE_2G);
  //lsm.setupAccel(lsm.LSM9DS0_ACCELRANGE_4G);
  //lsm.setupAccel(lsm.LSM9DS0_ACCELRANGE_6G);
  //lsm.setupAccel(lsm.LSM9DS0_ACCELRANGE_8G);
  lsm.setupAccel(lsm.LSM9DS0_ACCELRANGE_16G);
  
  // 2.) Set the magnetometer sensitivity
  lsm.setupMag(lsm.LSM9DS0_MAGGAIN_2GAUSS);
  //lsm.setupMag(lsm.LSM9DS0_MAGGAIN_4GAUSS);
  //lsm.setupMag(lsm.LSM9DS0_MAGGAIN_8GAUSS);
  //lsm.setupMag(lsm.LSM9DS0_MAGGAIN_12GAUSS);

  // 3.) Setup the gyroscope
  //lsm.setupGyro(lsm.LSM9DS0_GYROSCALE_245DPS);
  //lsm.setupGyro(lsm.LSM9DS0_GYROSCALE_500DPS);
  lsm.setupGyro(lsm.LSM9DS0_GYROSCALE_2000DPS);
}
 spiflash flash;

int sample_number;
  char mode;
int current_page;

void setup() 
{
  Serial.begin(BAUD);
  Serial.println("~~RocketAV software version 1.0~~");
  flash.init(MEM_EN);


  Serial.print("Please select: [i]dle mode, [l]aunch mode, [d]ownload data, [e]rase memory? ");
  if (!lsm.begin()) {
    Serial.println("Oops ... unable to initialize the LSM9DS0. Check your wiring!");
  }


  setupSensor();
  sample_number = 0;
  mode = 'i';
  flash.unprotect();
}

void loop() 
{
// Wait for USB port communication

  char input;
  int nextpage;
  if(Serial1)
  {
  if(Serial.available())
  { 
    input=Serial.read();
    switch (input)
    {
      case 'i':
        mode = 'i';
        Serial.println("Entering idle mode...");
        break;
      
      case 'l':
        mode = 'l';
        sample_number = 0;
        Serial.println("Entering launch mode...");
        Serial.println("Beginning 60s launch timer...");
        delay(120000);
        break;
        
      case 'd':
        nextpage = 0;
        for(int i = 0; i < PAGE_SIZE; i++) {pdata.bytes[i] = 0;}
        Serial.print("Reading from flash head at 0x");
        Serial.println(flash.getHead(), HEX);
        for(uint16_t i = 0; i < flash.getHead(); i++)
        {

//          Serial.print("Reading page ");
//          Serial.println(i);
          uint32_t addr = flash.readPage(i, pdata.bytes);
//          Serial.print("Actual address ");
//          Serial.println(addr, HEX);
          for (int j = 0; j < samples_per_page; j++)
          {
            serialPrintSample(pdata.entries[j]);
          }          
        };

        break;
      case 'e':
        Serial.print("Erasing memory... ");
        flash.chipErase();
        Serial.println("Done!");
        break;
      }
      Serial.print("Please select: [i]dle mode, [l]aunch mode, [d]ownload data, [e]rase memory? ");
    }
  }
    
  if (mode == 'i')
  {
    ;
  }  
  else if (mode == 'l')
  {
    delay(SENSOR_STALL);
    lsm.read();
    sensor_sample curr;

    curr.timestamp = millis();
    curr.xm_x = lsm.accelData.x;
    curr.xm_y = lsm.accelData.y;
    curr.xm_z = lsm.accelData.z;
    curr.gyr_x = lsm.gyroData.x;
    curr.gyr_y = lsm.gyroData.y;
    curr.gyr_z = lsm.gyroData.z;
    curr.mag_x = lsm.magData.x;
    curr.mag_y = lsm.magData.y;
    curr.mag_z = lsm.magData.z;
    curr.temp = lsm.temperature;
    curr.line = 0xA;
    pdata.entries[sample_number] = curr;

    #ifdef SERIAL_DEBUG
    if(Serial1)
    {
      Serial.print("Sample ");
      Serial.print(sample_number);
      Serial.print(":");
      serialPrintSample(curr);
    }
    #endif

    sample_number++;

    if(sample_number >= samples_per_page)
    {
      int err;
      err = flash.writeSequentialPage(pdata.bytes, PAGE_SIZE);
      
      sample_number = 0;
      for(int i = 0; i < PAGE_SIZE; i++) {pdata.bytes[i] = 0;}

    #ifdef SERIAL_DEBUG
    Serial.print("Printing page");
    Serial.println(err);
    Serial.print("Head location: ");
    Serial.println(flash.getHead(), HEX);
    Serial.print("Address equivalent: ");
    Serial.println(((uint32_t)flash.getHead()) << 8, HEX);
    #endif
    }

  }
}


void serialPrintSample(sensor_sample curr_data)
{
  Serial.print(curr_data.timestamp);
  Serial.print(',');
  Serial.print(curr_data.xm_x);
  Serial.print(',');
  Serial.print(curr_data.xm_y);
  Serial.print(',');   
  Serial.print(curr_data.xm_z);
  Serial.print(','); 
  Serial.print(curr_data.gyr_x);
  Serial.print(',');
  Serial.print(curr_data.gyr_y);
  Serial.print(',');
  Serial.print(curr_data.gyr_z);
  Serial.print(',');
  Serial.print(curr_data.mag_x);
  Serial.print(',');
  Serial.print(curr_data.mag_y);
  Serial.print(',');
  Serial.print(curr_data.mag_z);
  Serial.print(',');
  Serial.println(curr_data.temp);
}

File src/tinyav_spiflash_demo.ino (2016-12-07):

#include <tinyav_spiflash.h>

#define BAUD 115200

spiflash flash;


void setup() {
  Serial.begin(BAUD);

  // start the SPI library:
  SPI.begin();

  flash.init(FLASH_SS);
  
  SPI.beginTransaction(SPISettings(SPICLOCK, MSBFIRST, SPI_MODE0));

  // initalize the  data ready and chip select pins:
  pinMode(FLASH_SS, OUTPUT);
  digitalWrite(FLASH_SS, HIGH);
  pinMode(XM_SS, OUTPUT);
  digitalWrite(XM_SS, HIGH);
  pinMode(GYR_SS, OUTPUT);
  digitalWrite(GYR_SS, HIGH);
  flash.writeEnable();

  SPI.endTransaction();
  delay(5000);
}

void loop() 
{
  char input;
  if (Serial.available() > 0)
  {
    input = Serial.read();
    uint8_t buff[256];
    switch (input)
    {
      case 'e':
        Serial.print("Erasing chip... ");
        flash.chipErase();
        Serial.println("DONE");
        break;
      case 'r':
        flash.readBytes(0, buff, 256);
        for (int i = 0; i<256; i++)
        {
          Serial.print(buff[i], HEX);
          Serial.print('.');
        }
          Serial.println('\n');
          break;
        
      case 'A':
        buff[0] = 0xAA;
        buff[1] = 0xAA;
        flash.writeBytes(0, buff, 2);
        break;
      case 'B':
        buff[0] = 0xBB;
        buff[1] = 0xBB;
        flash.writeBytes(0, buff, 2);
        flash.writeBytes(2, buff, 2);
        break;
    }
  }
}

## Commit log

2016-10-22 Created Eagle project for schematic/layout
    [Main.sch]
2016-10-29 Updated master schematic to have power management front end.
2016-10-29 .... Actually added the .sch file this time.
    [Main.sch]
2016-10-30 Worked on schematic, connected memory
2016-10-30 Updated sensor connections on schematic.
    [Main.sch]
2016-10-30 Lifted flash memory unused pins in schematic
    [Main.sch]
2016-10-30 Almost finished schematic, left to be done:
    -Connect MUX to proper pins
    -Processor Interfacing
    -Still need to change USB connection
    -Finish footprints
    [Main.brd, Main.sch]
2016-10-31 Schematic reorganized and touched up
    [Main.brd, Main.sch]
2016-10-31 Minor changes to schematic power logic. Also added a couple bypass capacitors to output of LM317.
    [Main.sch]
2016-11-01 Added pin headers to read memory contents. Change before release!
    [Main.sch]
2016-11-02 ECE411: Began reworking schematic, removed cell protection and added LDO to library and schematic.
    [Main.sch]
2016-11-03 Replaced ATTiny with ATMega32U4. Hooked up LDO.
    [Lilypad_Arduino_USB_v12.brd, Lilypad_Arduino_USB_v12.sch, Main.sch]
2016-11-03 Added RESET switch and Oscillator to schematic
    [Main.sch]
2016-11-03 Re-made Main.brd file to reflect most recent schematic.
    [Main.brd]
2016-11-03 Commented changes to be made from design review, removed temp files
    [T08-Board.brd, T08-Schematic.sch]
2016-11-04 Added more design review notes
    [T08-Schematic.sch]
2016-11-04 Started library of custom footprints. LTC1998 comparator for undervoltage protection. User power switch.
    [T08-Schematic.sch]
2016-11-04 Changed to micro-USB B connector from SparkFun library
    [T08-Schematic.sch]
2016-11-05 Added RGB LED & resolved several ERC errors
    [T08-Schematic.sch]
2016-11-07 Connected interrupts and started layout
    [T08-Schematic.brd]
2016-11-07 Created ground plane, started draft layout, deleted temp files
    [T08-Schematic.brd, T08-Schematic.sch]
2016-11-08 Reworked layout a bit. Still need to connect memory and sensors.
2016-11-08 Finished board layout!! Still have to create ground planes and add ground vias, but other than that it's all done. Hooray!
    [T08-Schematic.brd]
2016-11-08 More layout work. All nodes connected, still need to run through DRC and deal with all that bs.
    [T08-Schematic.brd]
2016-11-08 Made some changes to silkscreen layer, fixed package text size.
    [T08-Schematic.brd]
2016-11-08 Finished preliminary board layout! Passed OSHParks DRC, hooray!
    [DRILEGEND.CFG, T08-Schematic.brd]
2016-11-09 Layout Review #1 With Andrew:
    -changed all 0805 packages to 0603 (made a lot more room)
    -made vias significantly smaller (made a lot more room)
    -updated layout to reflect these changes, no DRC issues
    We should consider hooking up the status pins of our battery charger to
    LEDs. Should also consider increasing the value of our current limiting
    resistors from the processor.
    [T08-Schematic.brd, T08-Schematic.sch]
2016-11-10 Updated a few oopsies on board layout. A couple nodes not connected, switch on bottom layer. Added a couple more vias as well.
    [T08-Schematic.brd]
2016-11-11 Added 3-pin pad for firing circuit
    [T08-Schematic.brd, T08-Schematic.sch]
2016-11-11 Kind of ugly, but I got the ignition switch hooked up.
    Should work alright! Board is ready to be shipped off!
    [T08-Schematic.brd]
2016-11-11 Updated current limiting resistors to 0805 package. Also fixed some oopsies on the layout (extra traces).
    [T08-Schematic.brd, T08-Schematic.sch]
2016-11-16 Added resistors to D+/D-, removed incorrect reset button cap, fixed RGB LED VCC
    [T08-Schematic.brd, T08-Schematic.sch]
2016-11-17 Lots of changes to layout!
    -Added 6 pin header
    -Added status LEDs
    -Added Power LEDs`
    [T08-Schematic.brd, T08-Schematic.sch]
2016-11-17 Added 0 ohm resistor to #HWB line. Added test points to unpopulated GPIO.
    [T08-Schematic.brd, T08-Schematic.sch]
2016-11-17 Added test points to accelerometer DRDY and DENB
    [T08-Schematic.brd, T08-Schematic.sch]
2016-11-17 Fixed silkscreen
    [T08-Schematic.brd]
2016-11-17 Some silk screen touches to BRD file.
    Ready to ship off.
    [T08-Schematic.brd]
2016-11-17 Removed confusing redundant board file
    [T08-Board.brd]
2016-11-24 Added PDF version of Schematic for reference purposes
2016-11-24 Made changes to schematic to display IC names
2016-11-28 Tried covering the ground vias with soldermask since they're exposed currently and it's making me go crazy I stay up late at night thinking about it.
    [T08-Schematic.brd]
2016-12-01 Reorganized Folders & Documentation. Changed documentation to be consistent with project name
    [DRILEGEND.CFG, Lilypad_Arduino_USB_v12.brd, Lilypad_Arduino_USB_v12.sch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]
2016-12-01 Added pdf for board layout
    [T08-Schematic.brd, T08-Schematic.sch]
2016-12-01 Re-added board file
    [T08-Schematic.brd]
2016-12-04 Rerouted /PG pin on BQ24022. Corrected symbol and added to eagle library.
    [T08-Schematic.brd, T08-Schematic.sch]
2016-12-04 Rearranged repo
    [DRILEGEND.CFG, Lilypad_Arduino_USB_v12.brd, Lilypad_Arduino_USB_v12.sch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]
2016-12-07 Uploaded custom SPI library source files
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2016-12-07 Added makefile to create zip for arduino libs
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2016-12-07 Makefile for generating Arduino zips. RocketAv script updated.
2016-12-07 Pushing for Aaron -
    Bug hunting main program sketch.
    [RocketAv.ino]
2016-12-07 Added Bill Of Materials
    [Bill_Of_Materials_xls.xlsx]
2016-12-07 Working main sketch. Fixed overflow, simplified spiflash library.
    [RocketAv.ino]
2016-12-08 Saved calibration data for xm, mag
    [accel_xcal.csv, accel_ycal.csv, accel_zcal.csv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]
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2016-12-08 Fixed bug with sensor calibration
    [RocketAv.ino]
2016-12-08 Formatted launch file correctly
    [lawndart_launch.csv]
2016-12-08 Fixed sensor cal bug
    [RocketAv.ino]
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2016-12-08 Reorganized cal data and corrected format. Added calibration scripts.
    [BlueGyro.csv, GreenGyro.csv]
2016-12-08 Added launch data for Thursday, 12/08/2016
    [08122016_launch1.csv, 08122016_launch2.csv, lawndart_launch.csv]
2016-12-08 Updated 'ref' ReadMe & moved BOM to correct location
2016-12-08 Fixed merge issues. Andy's a dingus.
    [RocketAv.ino]
2016-12-16 Added device for charging chip, and created footprint and device for sensor.
    Also began reworking schematic.
    [T08-Schematic.brd, T08-Schematic.sch]
2016-12-18 Reorganized files for transition to independent project
    [DRILEGEND.CFG, tiny-avionics.brd, tiny-avionics.sch]
2016-12-18 Reverted board files on master to known-good version
    [tiny-avionics.brd, tiny-avionics.sch]
2016-12-18 Schematic work and created new device for 8-pin SPI memory chip.
    [tiny-avionics.brd, tiny-avionics.sch]
2016-12-18 Working changes to schematic and layout.
    [tiny-avionics.brd, tiny-avionics.sch]
2016-12-21 Continued layout work.
    [tiny-avionics.brd, tiny-avionics.sch]
2016-12-21 More layout work. Removed a bypass capacitor we didn't really need.
    [tiny-avionics.brd, tiny-avionics.sch]
2016-12-22 Finished new board layout with no DRC errors.
    It's a little smaller, but not much smaller. Made an effort to spread out
    components for easier assembly, however. Layout is also much more
    intuitive.
    [tiny-avionics.brd, tiny-avionics.sch]
2016-12-23 Some minor changes.
    [tiny-avionics.brd]
2016-12-28 Added SMD crystal device and replaced on board
    [tiny-avionics.brd, tiny-avionics.sch]
2016-12-28 Added thermistor to bottom of board
    [tiny-avionics.brd, tiny-avionics.sch]
2017-01-01 Went through a few of the issues Andrew raised. Still some that need to be addressed.
    [tiny-avionics.brd, tiny-avionics.sch]
2017-01-11 Finished layout rework from 2nd design review.
    Still left to do:
    -Change 0603 footprints to RCL custom library 0603s
    -Additional schematic work
    [tiny-avionics.brd]
2017-02-04 Fixed remaining design rev issues. Slightly thinner pads for LSM6DS0 to comply with OshPark DRC.
    [tiny-avionics.brd, tiny-avionics.sch]
2017-02-15 Updated libraries, readme and file structure for Rev 2.0
    [old_Bill_Of_Materials_xls.xlsx, tiny-avionics.brd, tiny-avionics.sch]
2017-02-15 Added documentation from google drive. Added board and schematic images.
    [old_Bill_Of_Materials_xls.xlsx, tiny-avionics.sch]

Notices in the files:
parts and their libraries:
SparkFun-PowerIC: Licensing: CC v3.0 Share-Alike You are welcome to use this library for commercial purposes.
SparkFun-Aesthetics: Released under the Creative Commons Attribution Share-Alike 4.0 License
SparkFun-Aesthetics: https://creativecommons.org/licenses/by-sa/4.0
